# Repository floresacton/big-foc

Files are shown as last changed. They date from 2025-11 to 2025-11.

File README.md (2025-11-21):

# big-foc
Field Oriented Control Inverter

70V 160A 10kW continuous

12kW peak

99% efficiency at 8kW

48$ BOM + PCB Cost

65x75x32mm size

Ignoring the heatsink, that's 64kW/L :)

## Design Strategy

### 1. Power and Voltage Rating
- **Power Rating**: Target continuous and peak power
- **Battery Voltage**: 12S = 50.4V, 16S = 67.2V
- **Component Voltage Rating**: Components must be rated at >1.5x-2x battery voltage
  - Example: 16S battery (67.2V max) → 100V+ rated components minimum
  - Margin for voltage spikes, ringing
- **Thermal Limitation**: Max accepted power dissipation at continuous and peak power, <=100C

### 2. Power Stage Design

#### Switch Selection by Voltage
- **Low Voltage (<300V)**: MOSFETs
  - Aim for lower RDS(on) better conduction losses
  - Aim for lower total gate charge for better switching losses
  - Most cost-effective (100V rated components very common)
- **High Voltage (>300V)**: SiC FETs or IGBTs
  - SiC FETs: Fast switching, lower losses
  - IGBTs: Slower switching, higher switching losses, very high power

#### Gate Driver Selection
- **Bootstrap Drivers**: 
  - Simple, low cost
  - Requires minimum duty cycle for bootstrap to charge
  - Usually fine until back emf approaches battery voltage
  - Pick a fast reverse recovery charge diode
  
- **Isolated Drivers**:
  - Independent high-side supply
  - Usually for high-voltage (>300V)
  - Can handle 100% duty cycle
  - Expensive, more complex

### 3. Power Loss Analysis (very important)

#### Switching Losses
- Target switching frequency from 20-25khz (non audible range & less harmonic distortion)
- Transformers and motors are inductive loads (different switching waveforms than resistive switching loss)
- Switching loss ~= 1/2\*switching frequency\*current*voltage\*(t_on+t_off)
- t_on, t_off ~= Q_gate/I_charge
- I_charge = gate drive current

#### Conduction Losses
- I^2*R × rds_on (for mosfets)
- rds_on increases with temperature so we can use parallel FETs without runaway (thermals matter too)

### 4. Current Sensing

#### Sensing Approach
- **Phase count**:
  - Measure 2 phases calculate third (more noise)
  - Measure 3 phases and average (less noise, better if fits & symmetry)

- **In-Phase**:
  - Able to measures phase currents regardless of switch state
  - Higher cost, a lot of common mode noise
  - Better current measurements if done properly
  
- **Low-Side (1-3 shunts)**:
  - Cheaper
  - Simpler ground referenced amplifier design
  - Can only sample during low side conduction
  - Use stm32 timer ADC synchronization

#### Shunt Resistors
 - Should be around or slightly below rds_on of FETs
 - Good to have about 50-75mV at full current
 - Select for 20V/V amplifier (INA181A1 super common & cheap)
 - <=50ppm for 100C temp rise scenario
 - Need amplifier right next to shunt
 - Need center VREF amp for negative and positive current
 - Need to choose settling time to 1% better than 95% duty cycle (bootstrap is limiting factor)

#### Magnetic Sensing
- Hall-effect sensing built in packages
- Galvanic isolation included
- Higher cost, useful for very high currents
- Minimal power dissipation

### 5. Thermals

#### Power Dissipation Calculation
 - On average 2 half bridges are conducting fully, one is not conducting
- total switching loss ~= 4\*single switch loss
- gate charge loss is usually quite small compared to switching and resistive losses for 25khz
- total conduction loss ~= 2\*single conduction loss

#### FET Cooling Orientation
- **Top-Side Cooling**: FETs mounted with drain pad facing up
  - More expensive
  - Easier to cool and route
  
- **Bottom-Side Cooling**: FETs with dissipation through PCB
  - Cheaper
  - Easier assembly
  - Harder low inductance loop

#### Thermal Design Process
1. Calculate junction-to-case thermal resistance (datasheet)
2. Add PCB thermal resistance
3. Add heatsink thermal resistance
4. Junction temp = Ambient + (Total losses \* Total thermal resistance)
5. Target <100C but <60C is better

### 6. Protection and Sensing

#### Temperature Monitoring
- NTC thermistor (cheaper than PTC) on heatsink or FETs
- Lower B kind of better like 3400 because more linear over big range
- 10k 3400B ~= 1k at 100C, 30k at 0C

#### Fast Overvoltage Protection
- Hardware comparator for <1µs response time
- Trigger emergency PWM shutdown (stm32 timer break input)
- Threshold = 0.9% or something of voltage rating
- Directly disables gate drivers
- Optional avalanche diode for last resort protection

#### Voltage Measurement
- Resistor divider to ADC with a little bit of filtering
- Per-phase voltage for locking onto back emf for high speed

### 7. Microcontroller Selection

#### STM32G4 Series
**Key Features for FOC:**
- High-resolution timers with dead-time insertion and center aligned PWM
- Fast 12-bit ADCs
- ADC triggering synchronized to PWM for current sampling
- Multiple ADCs for simultaneous phase current sampling
- Math acceleration (FPU, CORDIC) for FOC
- Sufficient for >20kHz control loop

**Typical MCU Choices:**
- STM32G431: Small packages, cost-optimized
- STM32G474: More peripherals, flash, and RAM for complex algorithms

### 8. FOC Control Implementation

#### Control Loop Structure
- Current loop: 10-50kHz (1/10 of switching frequency typical)
- Velocity loop: 1-5kHz
- Position loop: 100-1000Hz

#### Key Considerations
- ADC sampling synchronized to PWM valley/center
- Current reconstruction for low-side shunts
- PI controller tuning based on motor parameters
- Clarke/Park transforms for coordinate conversion
- Space Vector Modulation (SVM) for efficient bus utilization
- Add third harmonic for higher effective bus voltage

### 9. PCB Layout (Very very important)
 - Low inductance switching loop
 - di/dt \* L = voltage induced over drain source
 - Low esr (usually MLCC) caps in low inductance switching loop
 - very rough calc Q_sustain = t_deadtime*I_peak
 - Q_sustain / V_spike = C_switch loop
 - Goal to hit V_spike <1% of V_bus
 - Keep loops as small as possible
 - Shunt amplifier right next to shunt resistor

### 10. Connectors
 - Waterproof, either SD13 series or DT Duetch (orange ones) are common
 - Phase and power wires just shrouded, bolt internally

### 11. Example Calculations (for my inverter)
- **Motor Characteristics**
	- 40uH phase to phase inductance
	- AMKs have 2.5nF inter winding capacitance
	- Couldn't find inter-winding capacitance of mine, but I think its relatively small losses compared to conduction
- [MOSFET loss equations](https://www.ti.com/lit/an/slyt664/slyt664.pdf?ts=1762657470589)
- [Layout and more equations](https://www.infineon.com/assets/row/public/documents/24/42/infineon-designing-an-optimized-half-bridge-dc-dc-converter-with-medium-voltage-coolgan-transistors-applic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)
 - **Losses**
	 - Power 8.4kW at 120A rms current or two phases at 170A
	 - 2 phases on at a time on average (same thing as 3 RMS currents)
	 - parallel rds @ 15V: 0.55mohm at 25C, 0.85mohm at 100C
	 - P_cond_tot = 2\*170\*170\*0.00055 = 32W
	 - P_shunt = 2\*170\*170\*0.00033 = 19W
	 - Q_gs2 = 20nC, Q_gd = 50nC, Q_eff = 70nC
	 - Q_actual = 140nC cause parallel FETs
	 - P_sw = 2\*70V\*170A\*25khz\*140nC/4A = 20.8W
	 - P_sw_total = 8.925W\*2 half bridge = 41.6W
     - P_recovery = 25khz\*200nC\*70V*8FETs = 2.8W
	 - P_coss = 12FETs \* 25khz \* 70V^2 \* 2.3nF = 3.4W
	 - P_winding_cap = 3 phase \* 25khz \* 70V^2 \* 2.5nF = 0.9W
	 - P_gate_total = 12 FETs\*250nC\*15V\*25khz = 1.1W
	 - P_gate_drive = <1W
	 - Deadtime 150ns
	 - P_diode = ~1.5\*1.2V\*170A\*25khz\*150ns = 1.2W (a bit sus math but reasonable)
	 - 4% dissipation factor for 1206 2.2uF ~ 10mohm I think for equivalent 10 (randomish number)
	 - Sw_energy = 70V\*170A\*140nC/4A = 0.4mJ per phase
	 - C_droop ~= 0.4mJ/(20uF \* 70V) = 0.3V
	 - The Vrms of the droop is prob below ~50mV
	 - P_cap_sw = 50mV^2/10mohm = 0.25W*3phases comes to <1W
	 - I_ripple ~= 110A
	 - Assuming 70A into ceramics and 40A into electrolytic
	 - 80 ceramics / 70A = 0.87A per ceramic
	 - P_ripple_cer = 0.875^2 \* 100mohm = 80mW
	 - P_cer_tot = 0.08*80 = 6.4W
	 - Electrolytic 3mohm at 25khz (susish think ok)
	 - I_elec ~= 40A/10 = 4A
	 - P_elec = 4A^2 \* 3mohm = 48mW
	 - P_elec_tot = 48mW \* 10 = 0.5W
	 - Total at 8.4kW = 32+41.6+1.1+1.2+1+1+6.4+0.5+3.4+19+2.8= 109.9W
	 - About 98.6% efficiency
- **Control**
	- Max phase current 220A, 210A max (170rms) is 12kW
	- SVPWM
	- Optional 3rd harmonic overmodulation
	- I_phase_rms = I_phase_pk / sqrt(12)
	- I_pk_pk_ripple = 70V / (2 \* 40uH \* 25khz) \* D \* (1-D) = 8.75A ; D=0.5
	- I_pk = 4.4A
	- I_rms = I_pk_pk_ripple / sqrt(12) = 2.5A

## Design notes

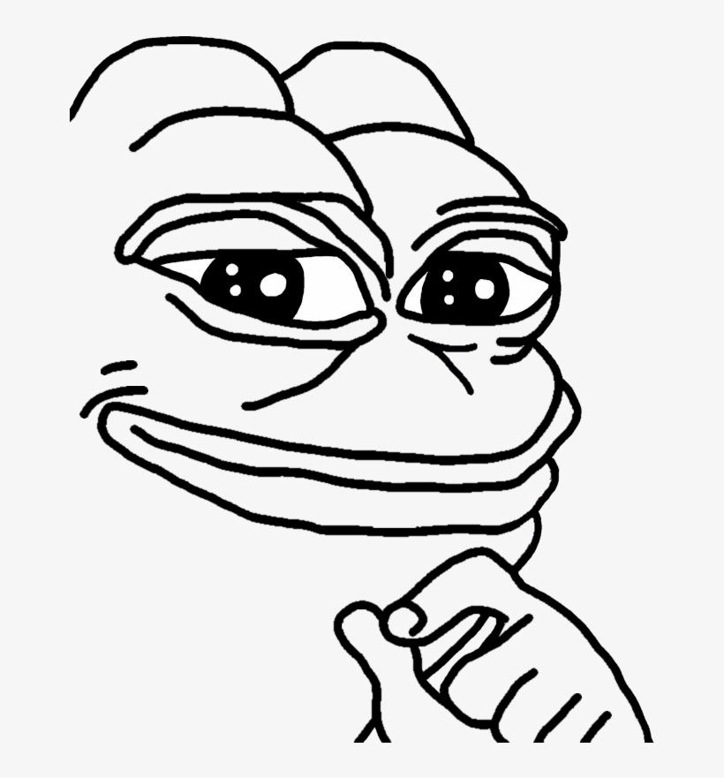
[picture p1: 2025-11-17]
pcb/logic/smart-pepe.jpg

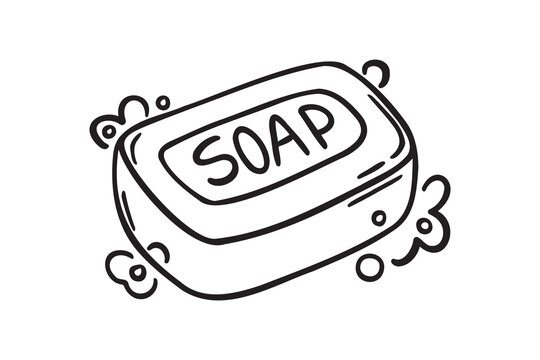
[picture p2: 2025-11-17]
pcb/logic/soap.jpg

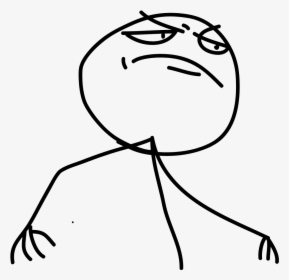
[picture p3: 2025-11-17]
pcb/logic/stickman-showoff.jpg

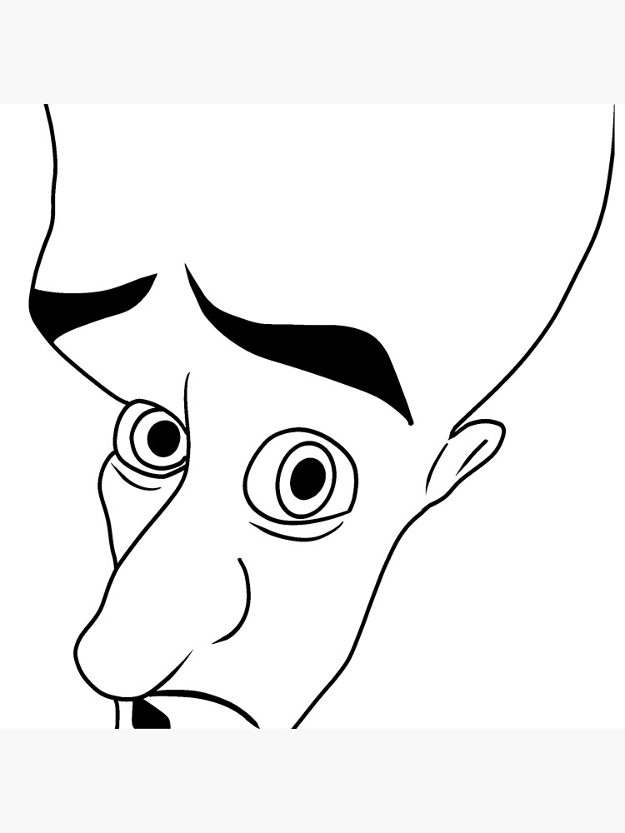
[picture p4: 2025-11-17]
pcb/logic/megamind.jpg

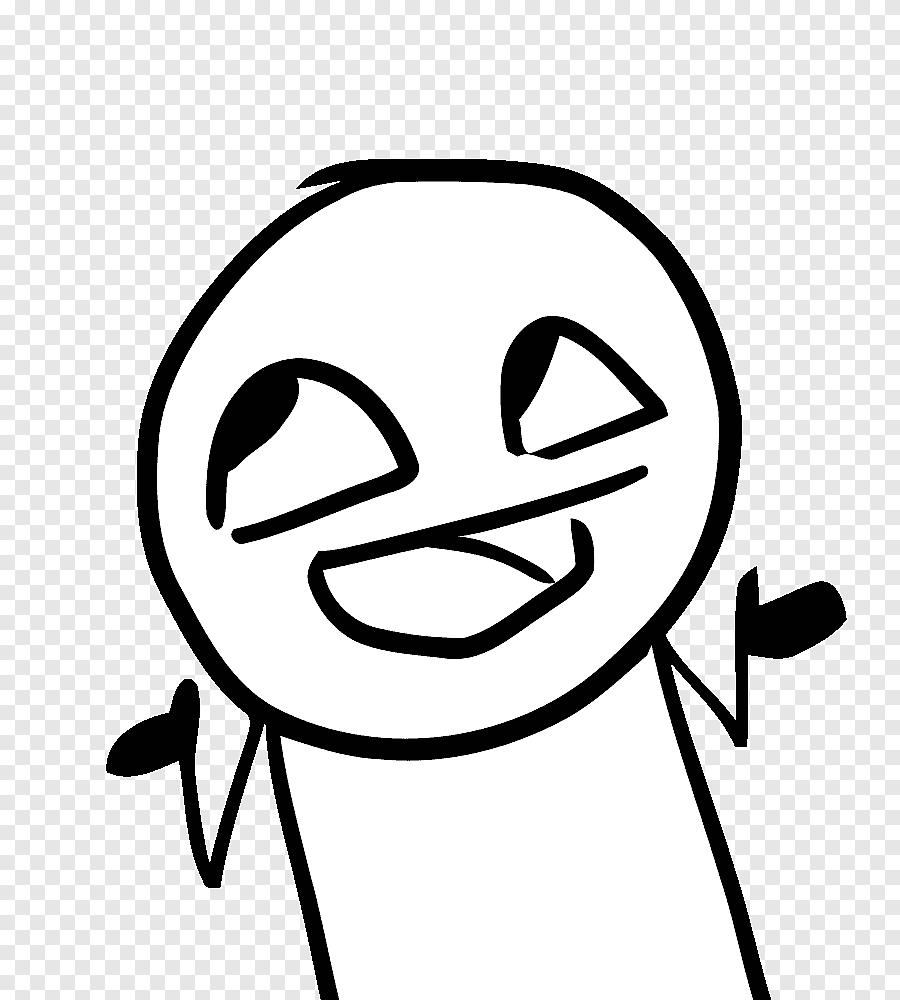
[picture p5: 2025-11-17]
pcb/logic/iguess.png

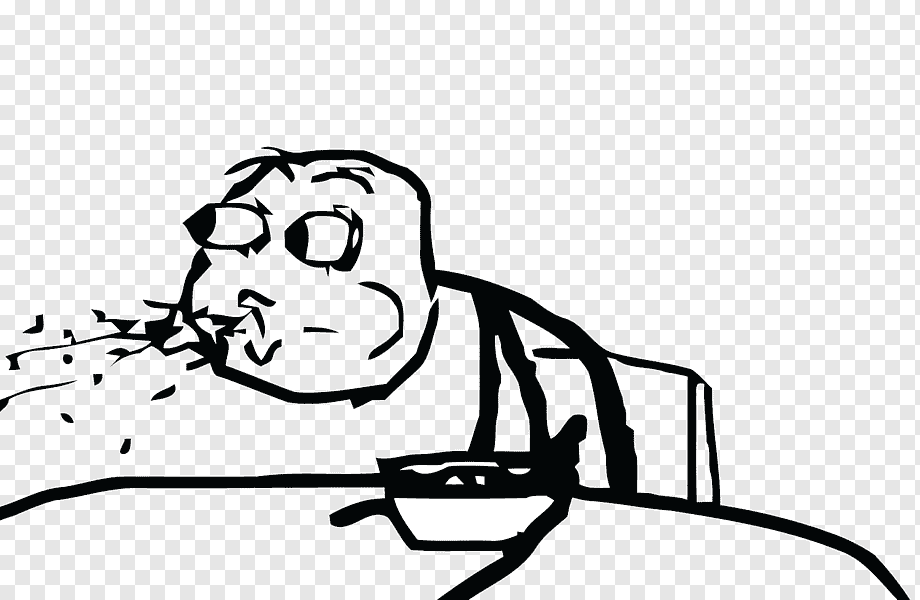
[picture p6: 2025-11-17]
pcb/logic/surprised.png

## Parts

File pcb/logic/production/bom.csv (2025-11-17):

Designator | Footprint | Quantity | Value | LCSC Part #
C1, C2, C3 | 1206 | 3 | 4u7 | C29823
C10, C11, C12, C13, C14, C15, C16, C19, C34, C35, C36, C37, C38, C39, C41, C42, C43, C44, C46, C47, C48, C49, C50, C52, C54, C55, C7, C8, C9 | 0402 | 29 | 100n | C307331
C17, C4, C5, C6 | 0402 | 4 | 220p | C1530
C18, C25, C26, C27, C28, C29, C30 | 0402 | 7 | 10n | C15195
C20, C40, C57 | 1206 | 3 | 22u | C20416445
C21, C22, C23, C24, C45, C56, C59 | 0805 | 7 | 4u7 | C33546011
C31, C32, C33, C58 | 0402 | 4 | 1n | C1523
C51, C53 | 0402 | 2 | 10p | C32949
D1 | 0603 | 1 | LED | C2290
D4, D5, D6 | D_SOD-323 | 3 | 1N4148WS | C2128
FB1 | 0603 | 1 | 120 | C14709
J1, J3, J5 | PinSocket_2x02_P1.27mm_Vertical_SMD | 3 | Conn_02x02_Odd_Even | C30607465
J2, J4, J6 | PinSocket_2x03_P1.27mm_Vertical_SMD | 3 | Conn_02x03_Odd_Even | C32713074
L2 | L_TechFuse_SL0420 | 1 | 4u7 | C22463808
R1, R11, R13, R2, R26, R27, R28, R3, R30, R33, R34 | 0402 | 11 | 33k | C25779
R10, R12, R14, R15, R16, R17, R29, R31, R35, R36, R37, R38, R4, R40, R41, R42, R43, R5, R6, R7, R8, R9 | 0402 | 22 | 2k2 | C25879
R18, R19, R20, R21, R22, R23 | 0603 | 6 | 1 | C22936
R24, R25 | 0805 | 2 | 51 | C17738
R32 | 0402 | 1 | 330 | C25104
R39 | 0402 | 1 | 12k | C25752
TH1, TH2, TH3, TH4 | 0402 | 4 | 10k | C41417281
U1, U2, U3 | JEITA_SOIC-8_3.9x4.9mm_P1.27mm | 3 | IRS2181STR | C20623180
U10, U11, U12, U13, U8, U9 | SOT-23-5 | 6 | 74LVC1G66 | C46553572
U14 | SOT-23-6 | 1 | JW5017S | C371172
U4 | SOT-223-3_TabPin2 | 1 | AMS1117-3.3 | C6186
U5 | LQFP-48_7x7mm_P0.5mm | 1 | STM32G473CBTx | C730111
U6 | JEITA_SOIC-8_3.9x4.9mm_P1.27mm | 1 | SP485E | C6855
Y1 | Crystal_SMD_3225-4Pin_3.2x2.5mm | 1 | 16MHz | C13738

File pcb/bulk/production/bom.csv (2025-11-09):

Designator | Footprint | Quantity | Value | LCSC Part #
C1, C10, C11, C12, C13, C14, C15, C16, C17, C18, C19, C2, C20, C21, C22, C23, C24, C25, C26, C27, C28, C29, C3, C30, C31, C32, C33, C34, C35, C36, C37, C38, C39, C4, C40, C41, C42, C43, C44, C45, C46, C47, C48, C49, C5, C50, C51, C52, C53, C54, C55, C56, C57, C58, C59, C6, C60, C61, C62, C63, C64, C65, C66, C67, C68, C69, C7, C70, C71, C72, C73, C74, C75, C76, C77, C78, C79, C8, C80, C81, C9 | 1206 | 81 | 2u2 | C920964
C82, C83, C84, C85, C86 | C_Radial_D10.0mm_H20.0mm_P5.00mm | 5 | 100u | C106541
C87, C88, C89, C90, C91, C92, C93, C94 | C_Radial_D12.5mm_H20.0mm_P5.00mm | 8 | 220u | C5213780

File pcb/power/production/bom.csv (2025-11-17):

Designator | Footprint | Quantity | Value | LCSC Part #
C1, C11, C21 | 0402 | 3 | 100n | C1525
C10, C12, C13, C14, C15, C16, C17, C18, C19, C2, C20, C22, C23, C24, C25, C26, C27, C28, C29, C3, C30, C4, C5, C6, C7, C8, C9 | 1206 | 27 | 2u2 | C920964
J1, J3, J5 | PinHeader_2x02_P1.27mm_Vertical_SMD | 3 | Conn_02x02_Odd_Even | C27985143
J2, J4, J6 | PinHeader_2x03_P1.27mm_Vertical_SMD | 3 | Conn_02x03_Odd_Even | C27985144
Q1, Q10, Q11, Q12, Q2, Q3, Q4, Q5, Q6, Q7, Q8, Q9 | Infineon_PG-HSOF-8-1 | 12 | SP010N01BGHTO | C22385350
R1, R2, R3, R4, R5, R6, R7, R8, R9 | R_Shunt_3921 | 9 | 1m | C2927603
U1, U2, U3 | SOT-23-6 | 3 | INA181 | C52097916

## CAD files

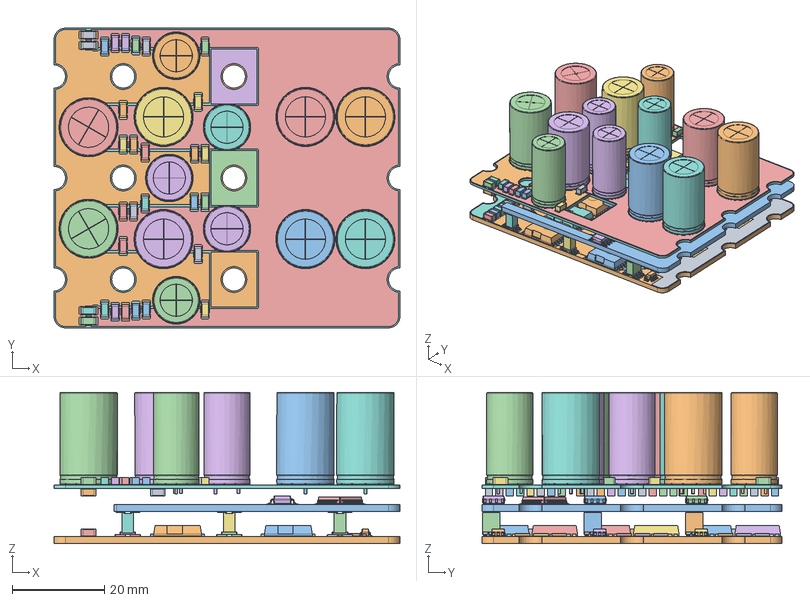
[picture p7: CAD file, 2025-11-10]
pcb/assembly.fcstd
75.0 x 65.0 x 32.8 mm
PinHeader_2x03_P1.27mm_Vertical_SMD
C_1206_3216Metric081
C_1206_3216Metric082
C_1206_3216Metric083
power 1.5.1
power 1.5.002
power 1.5.003
power 1.5.004
power 1.5.005
power 1.5.006
power 1.5.007
power 1.5.008
power 1.5.009
power 1.5.010
R_2512_6332Metric
power 1.5.012
power 1.5.013
power 1.5.014
power 1.5.015
power 1.5.016
power 1.5.017
power 1.5.018
power 1.5.019
power 1.5.020
power 1.5.021
R_2512_6332Metric001
power 1.5.023
power 1.5.024
power 1.5.025
power 1.5.026
power 1.5.027
power 1.5.028
power 1.5.029
power 1.5.030
power 1.5.031
power 1.5.032
C_1206_3216Metric084
C_1206_3216Metric085
power 1.5.034
power 1.5.035
power 1.5.036
power 1.5.037
power 1.5.038
power 1.5.039
power 1.5.040
power 1.5.041
power 1.5.042
power 1.5.043
C_1206_3216Metric086
power 1.5.045
power 1.5.046
power 1.5.047
power 1.5.048
power 1.5.049
power 1.5.050
power 1.5.051
power 1.5.052
power 1.5.053
power 1.5.054
C_1206_3216Metric087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

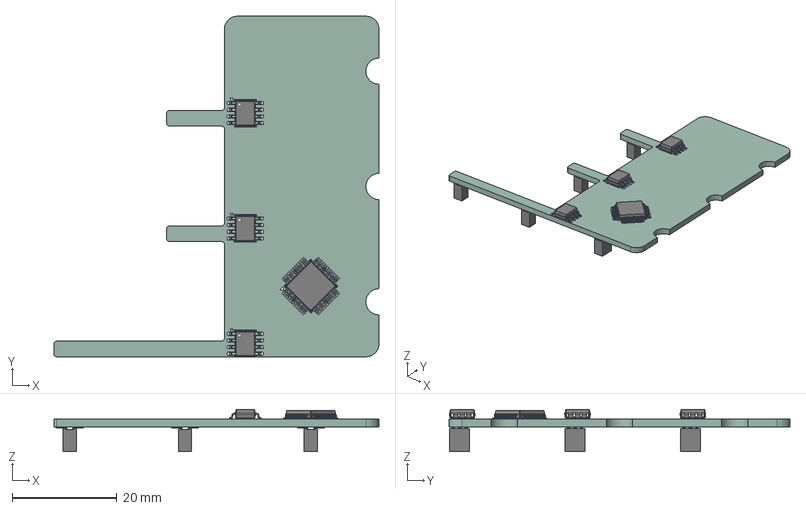
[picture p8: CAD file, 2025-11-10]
pcb/logic/logic.step
62.0 x 65.0 x 8.04 mm
SOIC-8_3.9x4.9mm_P1.27mm x 3
LQFP-48_7x7mm_P0.5mm
PinSocket_2x02_P1.27mm_Vertical_SMD x 4
PinSocket_2x03_P1.27mm_Vertical_SMD x 3
logic_pad
logic_silkscreen x 2
logic_PCB

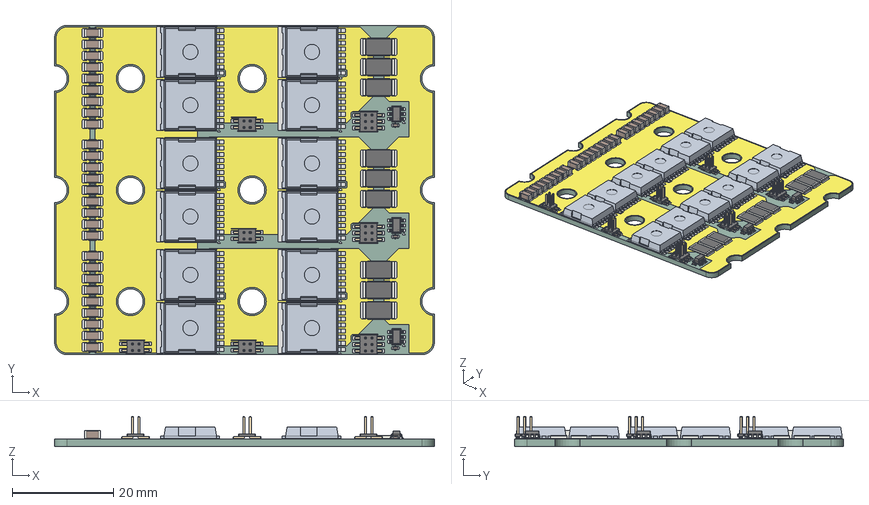
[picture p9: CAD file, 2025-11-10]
pcb/power/power.step
75.0 x 65.0 x 5.99 mm
PinHeader_2x03_P1.27mm_Vertical_SMD x 3
C_1206_3216Metric x 27
power 1.5.1 x 12
R_2512_6332Metric x 9
C_0402_1005Metric x 3
PinHeader_2x02_P1.27mm_Vertical_SMD x 4
SOT-23-6 x 3
power_copper
power_pad
power_silkscreen
power_PCB

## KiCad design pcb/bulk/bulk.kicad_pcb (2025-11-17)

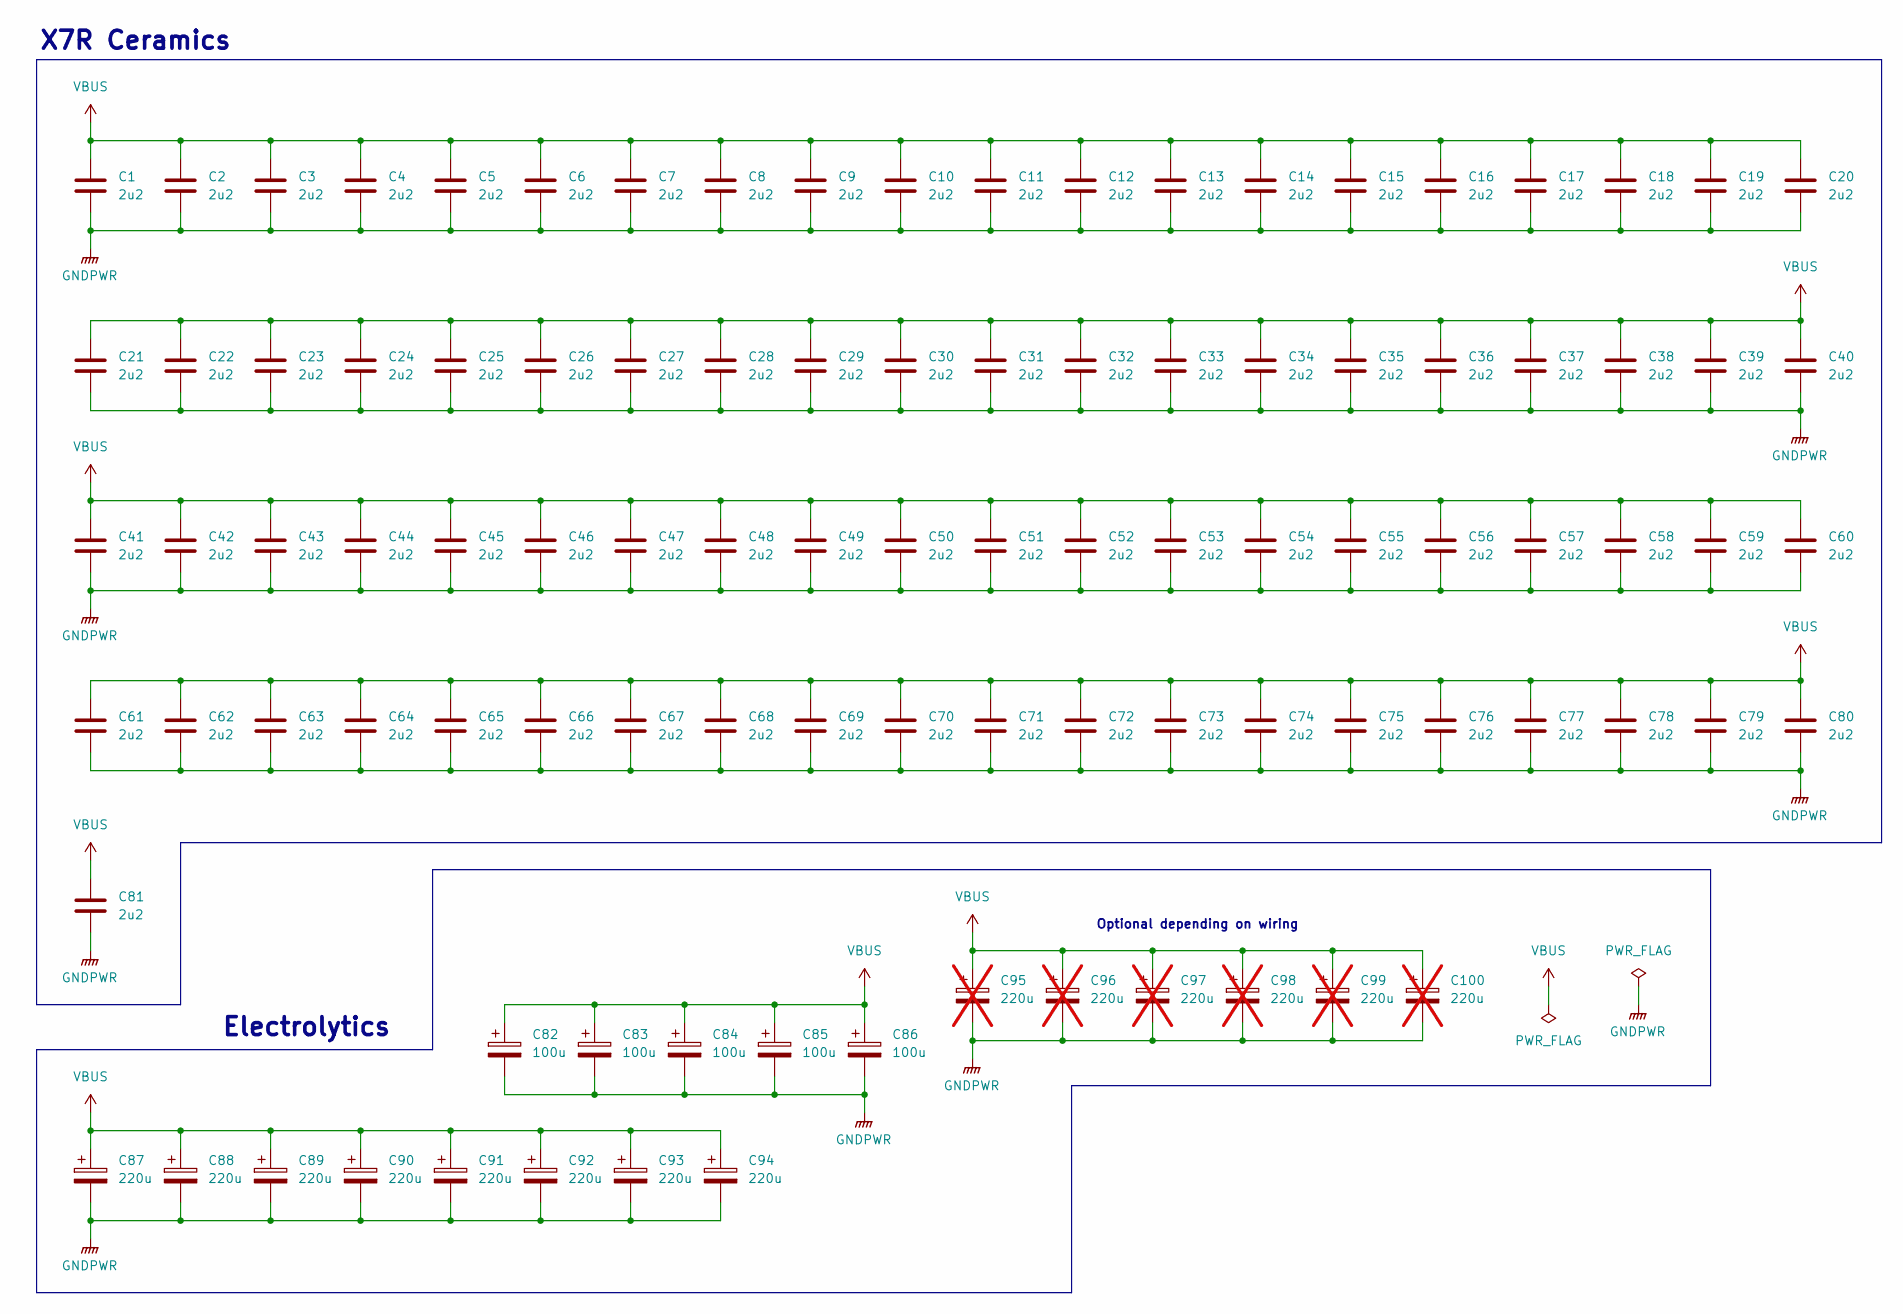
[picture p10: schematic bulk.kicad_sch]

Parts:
C1, C2, C3, C4, C5, C6, C7, C8, C9, C10, C11, C12, C13, C14, C15, C16, C17, C18, C19, C20, C21, C22, C23, C24, C25, C26, C27, C28, C29, C30, C31, C32, C33, C34, C35, C36, C37, C38, C39, C40, C41, C42, C43, C44, C45, C46, C47, C48, C49, C50, C51, C52, C53, C54, C55, C56, C57, C58, C59, C60, C61, C62, C63, C64, C65, C66, C67, C68, C69, C70, C71, C72, C73, C74, C75, C76, C77, C78, C79, C80, C81: 2u2; C_1206_3216Metric; LCSC C920964
C82, C83, C84, C85, C86: 100u; C_Radial_D10.0mm_H20.0mm_P5.00mm; LCSC C106541
C87, C88, C89, C90, C91, C92, C93, C94: 220u; C_Radial_D12.5mm_H20.0mm_P5.00mm; LCSC C5213780
C95, C96, C97, C98, C99, C100: 220u; C_Radial_D12.5mm_H20.0mm_P5.00mm; LCSC C5213780; not fitted

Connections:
GNDPWR: C1.2, C2.2, C3.2, C4.2, C5.2, C6.2, C7.2, C8.2, C9.2, C10.2, C11.2, C12.2, C13.2, C14.2, C15.2, C16.2, C17.2, C18.2, C19.2, C20.2, C21.2, C22.2, C23.2, C24.2, C25.2, C26.2, C27.2, C28.2, C29.2, C30.2, C31.2, C32.2, C33.2, C34.2, C35.2, C36.2, C37.2, C38.2, C39.2, C40.2, C41.2, C42.2, C43.2, C44.2, C45.2, C46.2, C47.2, C48.2, C49.2, C50.2, C51.2, C52.2, C53.2, C54.2, C55.2, C56.2, C57.2, C58.2, C59.2, C60.2, C61.2, C62.2, C63.2, C64.2, C65.2, C66.2, C67.2, C68.2, C69.2, C70.2, C71.2, C72.2, C73.2, C74.2, C75.2, C76.2, C77.2, C78.2, C79.2, C80.2, C81.2, C82.2, C83.2, C84.2, C85.2, C86.2, C87.2, C88.2, C89.2, C90.2, C91.2, C92.2, C93.2, C94.2, C95.2, C96.2, C97.2, C98.2, C99.2, C100.2
VBUS: C1.1, C2.1, C3.1, C4.1, C5.1, C6.1, C7.1, C8.1, C9.1, C10.1, C11.1, C12.1, C13.1, C14.1, C15.1, C16.1, C17.1, C18.1, C19.1, C20.1, C21.1, C22.1, C23.1, C24.1, C25.1, C26.1, C27.1, C28.1, C29.1, C30.1, C31.1, C32.1, C33.1, C34.1, C35.1, C36.1, C37.1, C38.1, C39.1, C40.1, C41.1, C42.1, C43.1, C44.1, C45.1, C46.1, C47.1, C48.1, C49.1, C50.1, C51.1, C52.1, C53.1, C54.1, C55.1, C56.1, C57.1, C58.1, C59.1, C60.1, C61.1, C62.1, C63.1, C64.1, C65.1, C66.1, C67.1, C68.1, C69.1, C70.1, C71.1, C72.1, C73.1, C74.1, C75.1, C76.1, C77.1, C78.1, C79.1, C80.1, C81.1, C82.1, C83.1, C84.1, C85.1, C86.1, C87.1, C88.1, C89.1, C90.1, C91.1, C92.1, C93.1, C94.1, C95.1, C96.1, C97.1, C98.1, C99.1, C100.1

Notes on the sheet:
X7R Ceramics
Optional depending on wiring
Electrolytics

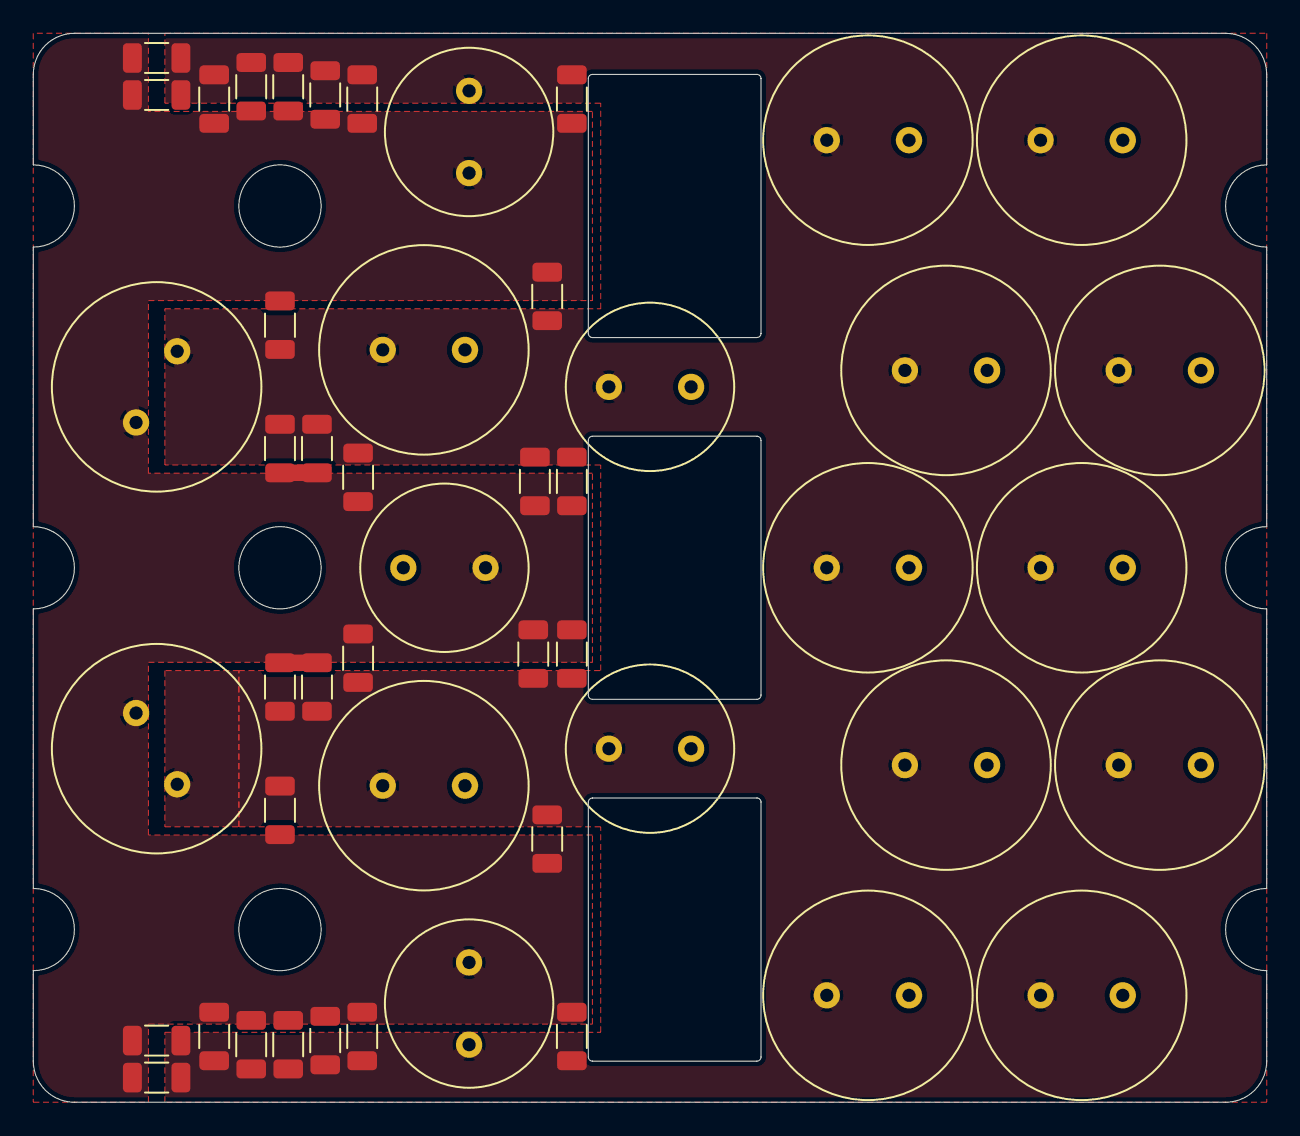
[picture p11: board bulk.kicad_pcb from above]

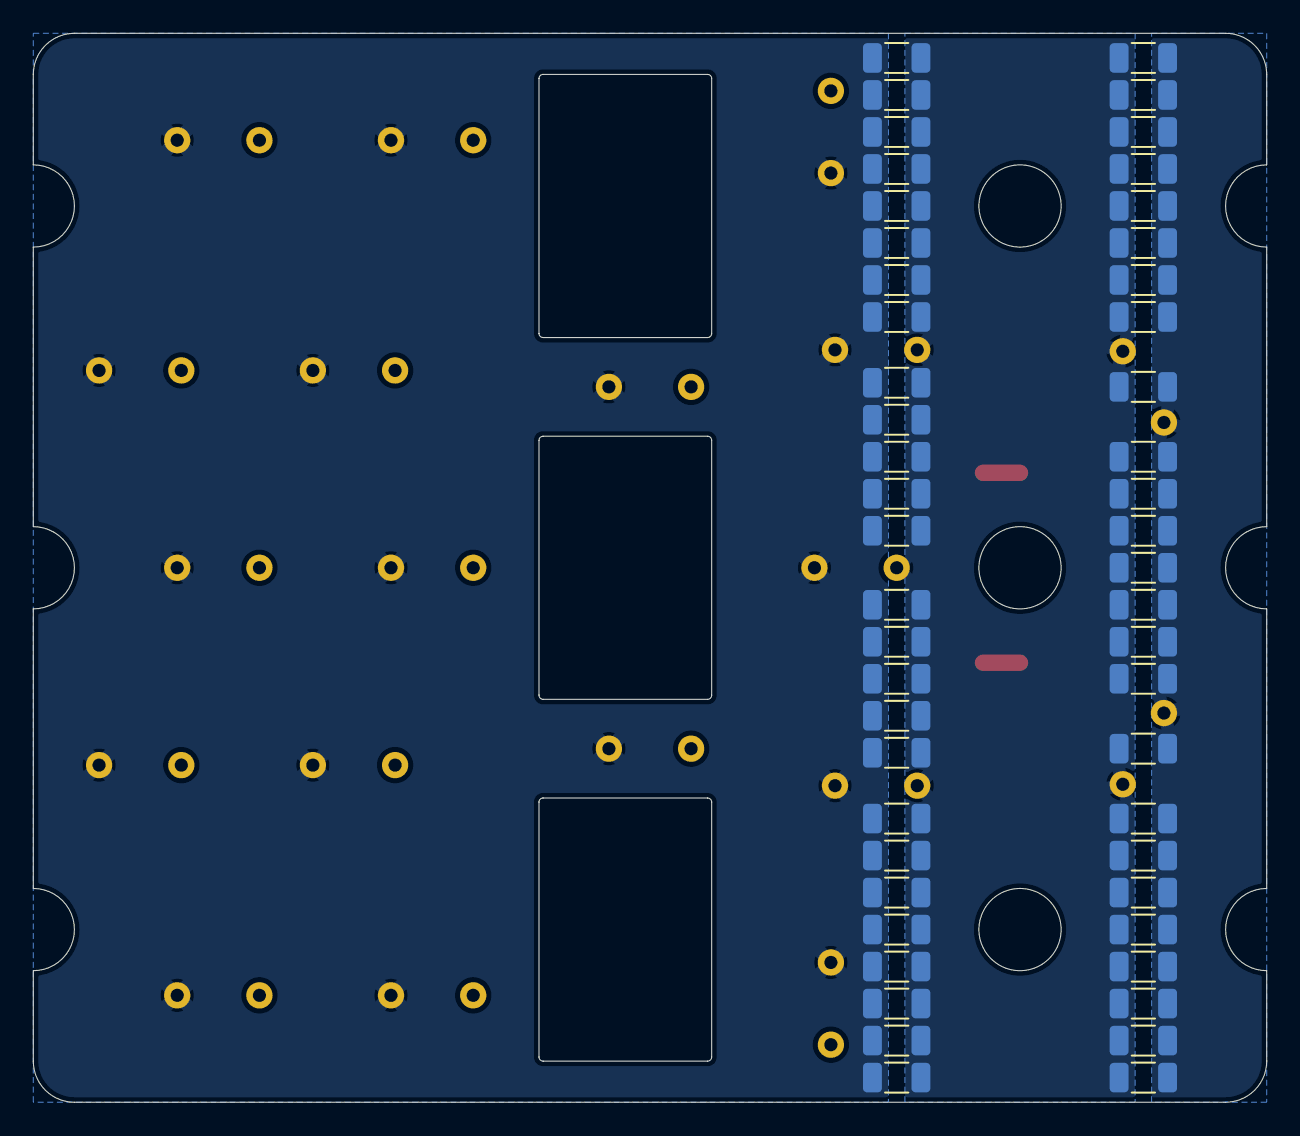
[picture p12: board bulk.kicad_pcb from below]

Board: 2 copper layers, 75.0 x 65.0 mm, 100 parts (51 on the bottom side), 2 nets.

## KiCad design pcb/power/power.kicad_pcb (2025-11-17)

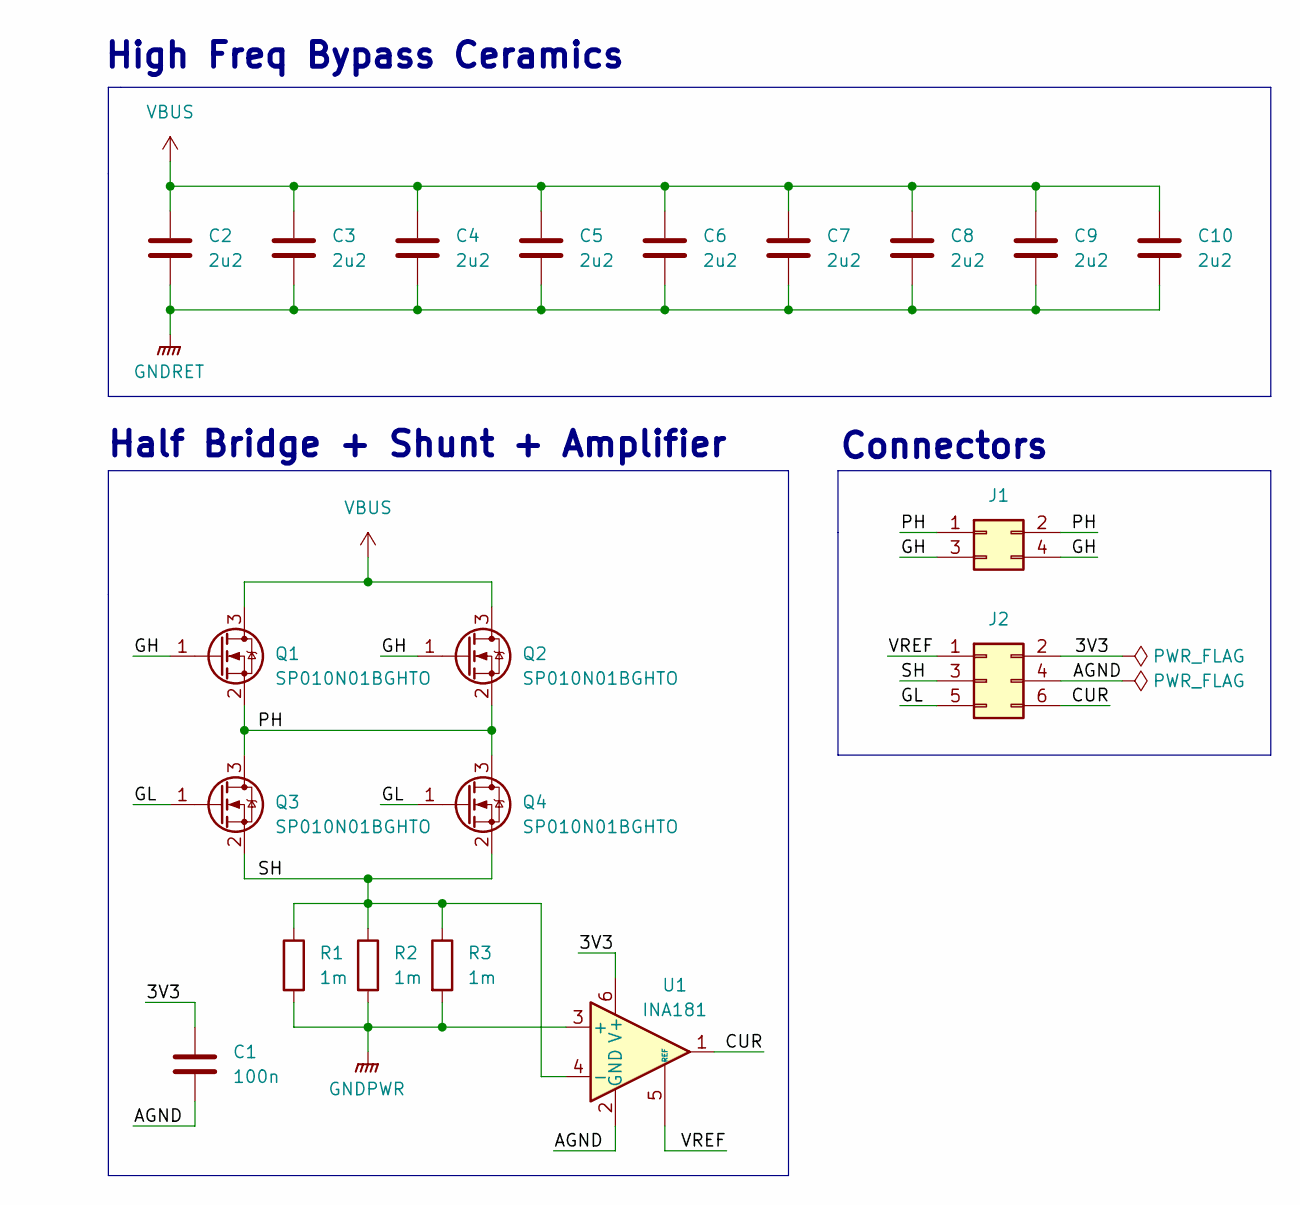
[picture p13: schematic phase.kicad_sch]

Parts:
C1: 100n; C_0402_1005Metric; LCSC C307331
C2, C3, C4, C5, C6, C7, C8, C9, C10: 2u2; C_1206_3216Metric; LCSC C920964
J1: Conn_02x02_Odd_Even; PinHeader_2x02_P1.27mm_Vertical_SMD; LCSC C27985143
J2: Conn_02x03_Odd_Even; PinHeader_2x03_P1.27mm_Vertical_SMD; LCSC C27985144
Q1, Q2, Q3, Q4: SP010N01BGHTO; Infineon_PG-HSOF-8-1; LCSC C22385350
R1, R2, R3: 1m; R_Shunt_3921; LCSC C2927603
U1: INA181; SOT-23-6; LCSC C52097916

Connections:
/Phase1/3V3: C1.1, J2.2, U1.6 (V+)
/Phase1/AGND: C1.2, J2.4, U1.2 (GND)
/Phase1/CUR: J2.6, U1.1
/Phase1/GH: J1.3, J1.4, Q1.1 (G), Q2.1 (G)
/Phase1/GL: J2.5, Q3.1 (G), Q4.1 (G)
/Phase1/PH: J1.1, J1.2, Q1.2 (S), Q2.2 (S), Q3.3 (D), Q4.3 (D)
/Phase1/SH: J2.3, Q3.2 (S), Q4.2 (S), R1.1, R2.1, R3.1, U1.4 (-)
/Phase1/VREF: J2.1, U1.5 (REF)
GNDPWR: R1.2, R2.2, R3.2, U1.3 (+); also elsewhere on the board
GNDRET: C2.2, C3.2, C4.2, C5.2, C6.2, C7.2, C8.2, C9.2, C10.2; also elsewhere on the board
VBUS: C2.1, C3.1, C4.1, C5.1, C6.1, C7.1, C8.1, C9.1, C10.1, Q1.3 (D), Q2.3 (D); also elsewhere on the board

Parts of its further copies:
C11, C21: 100n; C_0402_1005Metric; LCSC C307331
C12, C13, C14, C15, C16, C17, C18, C19, C20, C22, C23, C24, C25, C26, C27, C28, C29, C30: 2u2; C_1206_3216Metric; LCSC C920964
J3, J5: Conn_02x02_Odd_Even; PinHeader_2x02_P1.27mm_Vertical_SMD; LCSC C27985143
J4, J6: Conn_02x03_Odd_Even; PinHeader_2x03_P1.27mm_Vertical_SMD; LCSC C27985144
Q5, Q6, Q7, Q8, Q9, Q10, Q11, Q12: SP010N01BGHTO; Infineon_PG-HSOF-8-1; LCSC C22385350
R4, R5, R6, R7, R8, R9: 1m; R_Shunt_3921; LCSC C2927603
U2, U3: INA181; SOT-23-6; LCSC C52097916

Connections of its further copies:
/Phase2/3V3: C11.1, J4.2, U2.6 (V+)
/Phase2/AGND: C11.2, J4.4, U2.2 (GND)
/Phase2/CUR: J4.6, U2.1
/Phase2/GH: J3.3, J3.4, Q5.1 (G), Q6.1 (G)
/Phase2/GL: J4.5, Q7.1 (G), Q8.1 (G)
/Phase2/PH: J3.1, J3.2, Q5.2 (S), Q6.2 (S), Q7.3 (D), Q8.3 (D)
/Phase2/SH: J4.3, Q7.2 (S), Q8.2 (S), R4.1, R5.1, R6.1, U2.4 (-)
/Phase2/VREF: J4.1, U2.5 (REF)
/Phase3/3V3: C21.1, J6.2, U3.6 (V+)
/Phase3/AGND: C21.2, J6.4, U3.2 (GND)
/Phase3/CUR: J6.6, U3.1
/Phase3/GH: J5.3, J5.4, Q9.1 (G), Q10.1 (G)
/Phase3/GL: J6.5, Q11.1 (G), Q12.1 (G)
/Phase3/PH: J5.1, J5.2, Q9.2 (S), Q10.2 (S), Q11.3 (D), Q12.3 (D)
/Phase3/SH: J6.3, Q11.2 (S), Q12.2 (S), R7.1, R8.1, R9.1, U3.4 (-)
/Phase3/VREF: J6.1, U3.5 (REF)
GNDPWR: R4.2, R5.2, R6.2, R7.2, R8.2, R9.2, U2.3 (+), U3.3 (+); also elsewhere on the board
GNDRET: C12.2, C13.2, C14.2, C15.2, C16.2, C17.2, C18.2, C19.2, C20.2, C22.2, C23.2, C24.2, C25.2, C26.2, C27.2, C28.2, C29.2, C30.2; also elsewhere on the board
VBUS: C12.1, C13.1, C14.1, C15.1, C16.1, C17.1, C18.1, C19.1, C20.1, C22.1, C23.1, C24.1, C25.1, C26.1, C27.1, C28.1, C29.1, C30.1, Q5.3 (D), Q6.3 (D), Q9.3 (D), Q10.3 (D); also elsewhere on the board

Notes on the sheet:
High Freq Bypass Ceramics
Connectors
Half Bridge + Shunt + Amplifier

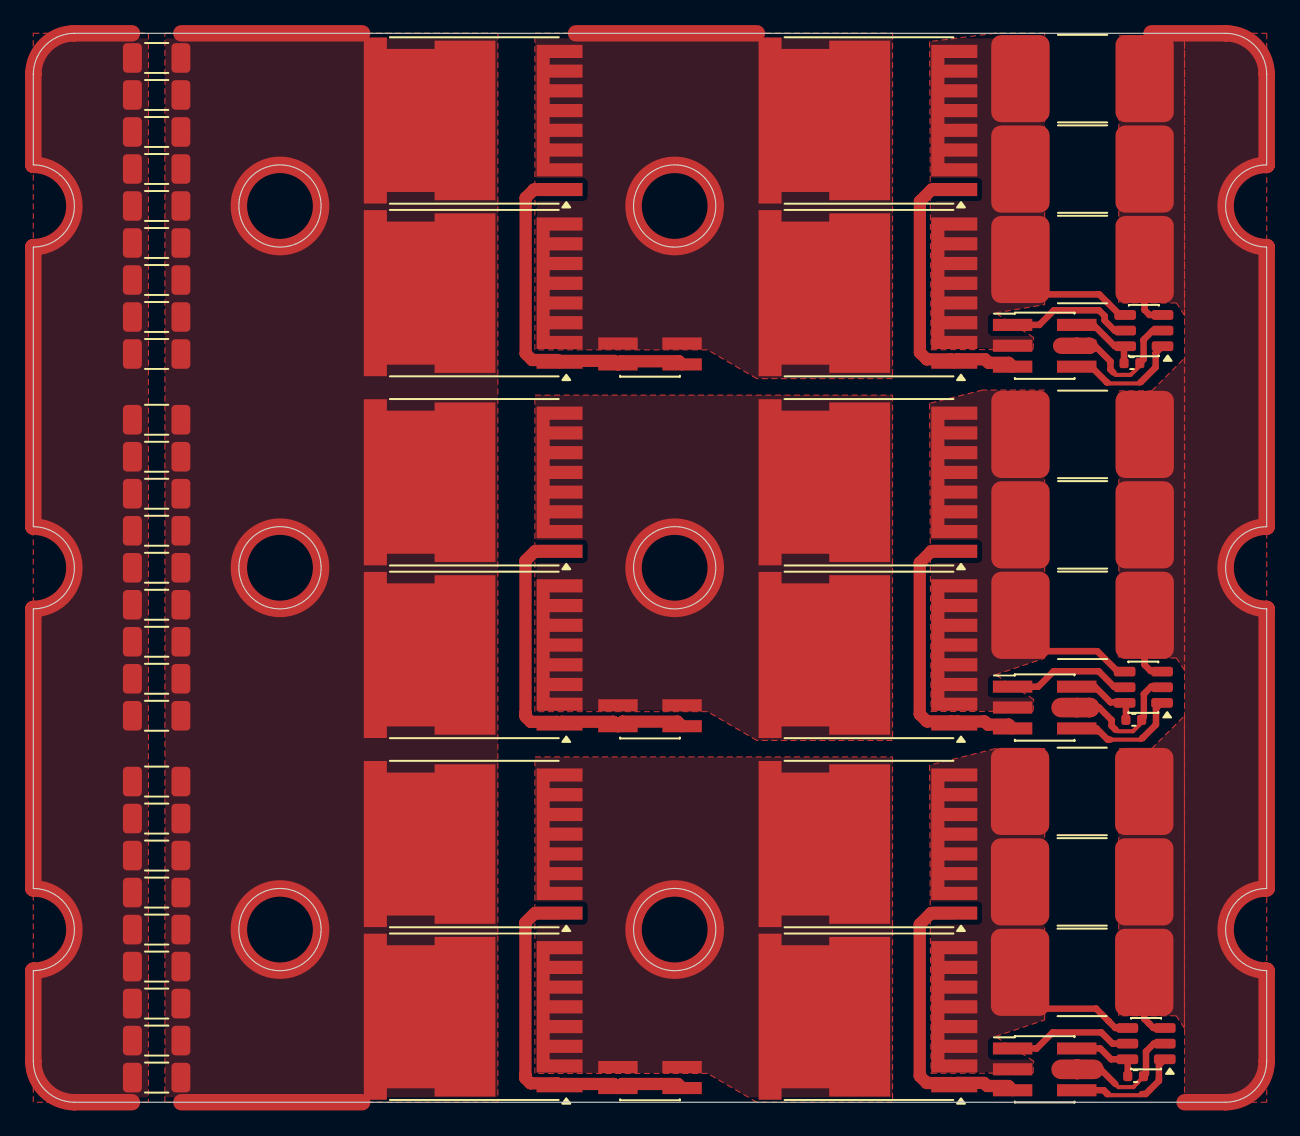
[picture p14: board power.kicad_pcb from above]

Board: 2 copper layers, 75.0 x 65.0 mm, 60 parts (0 on the bottom side), 27 nets.

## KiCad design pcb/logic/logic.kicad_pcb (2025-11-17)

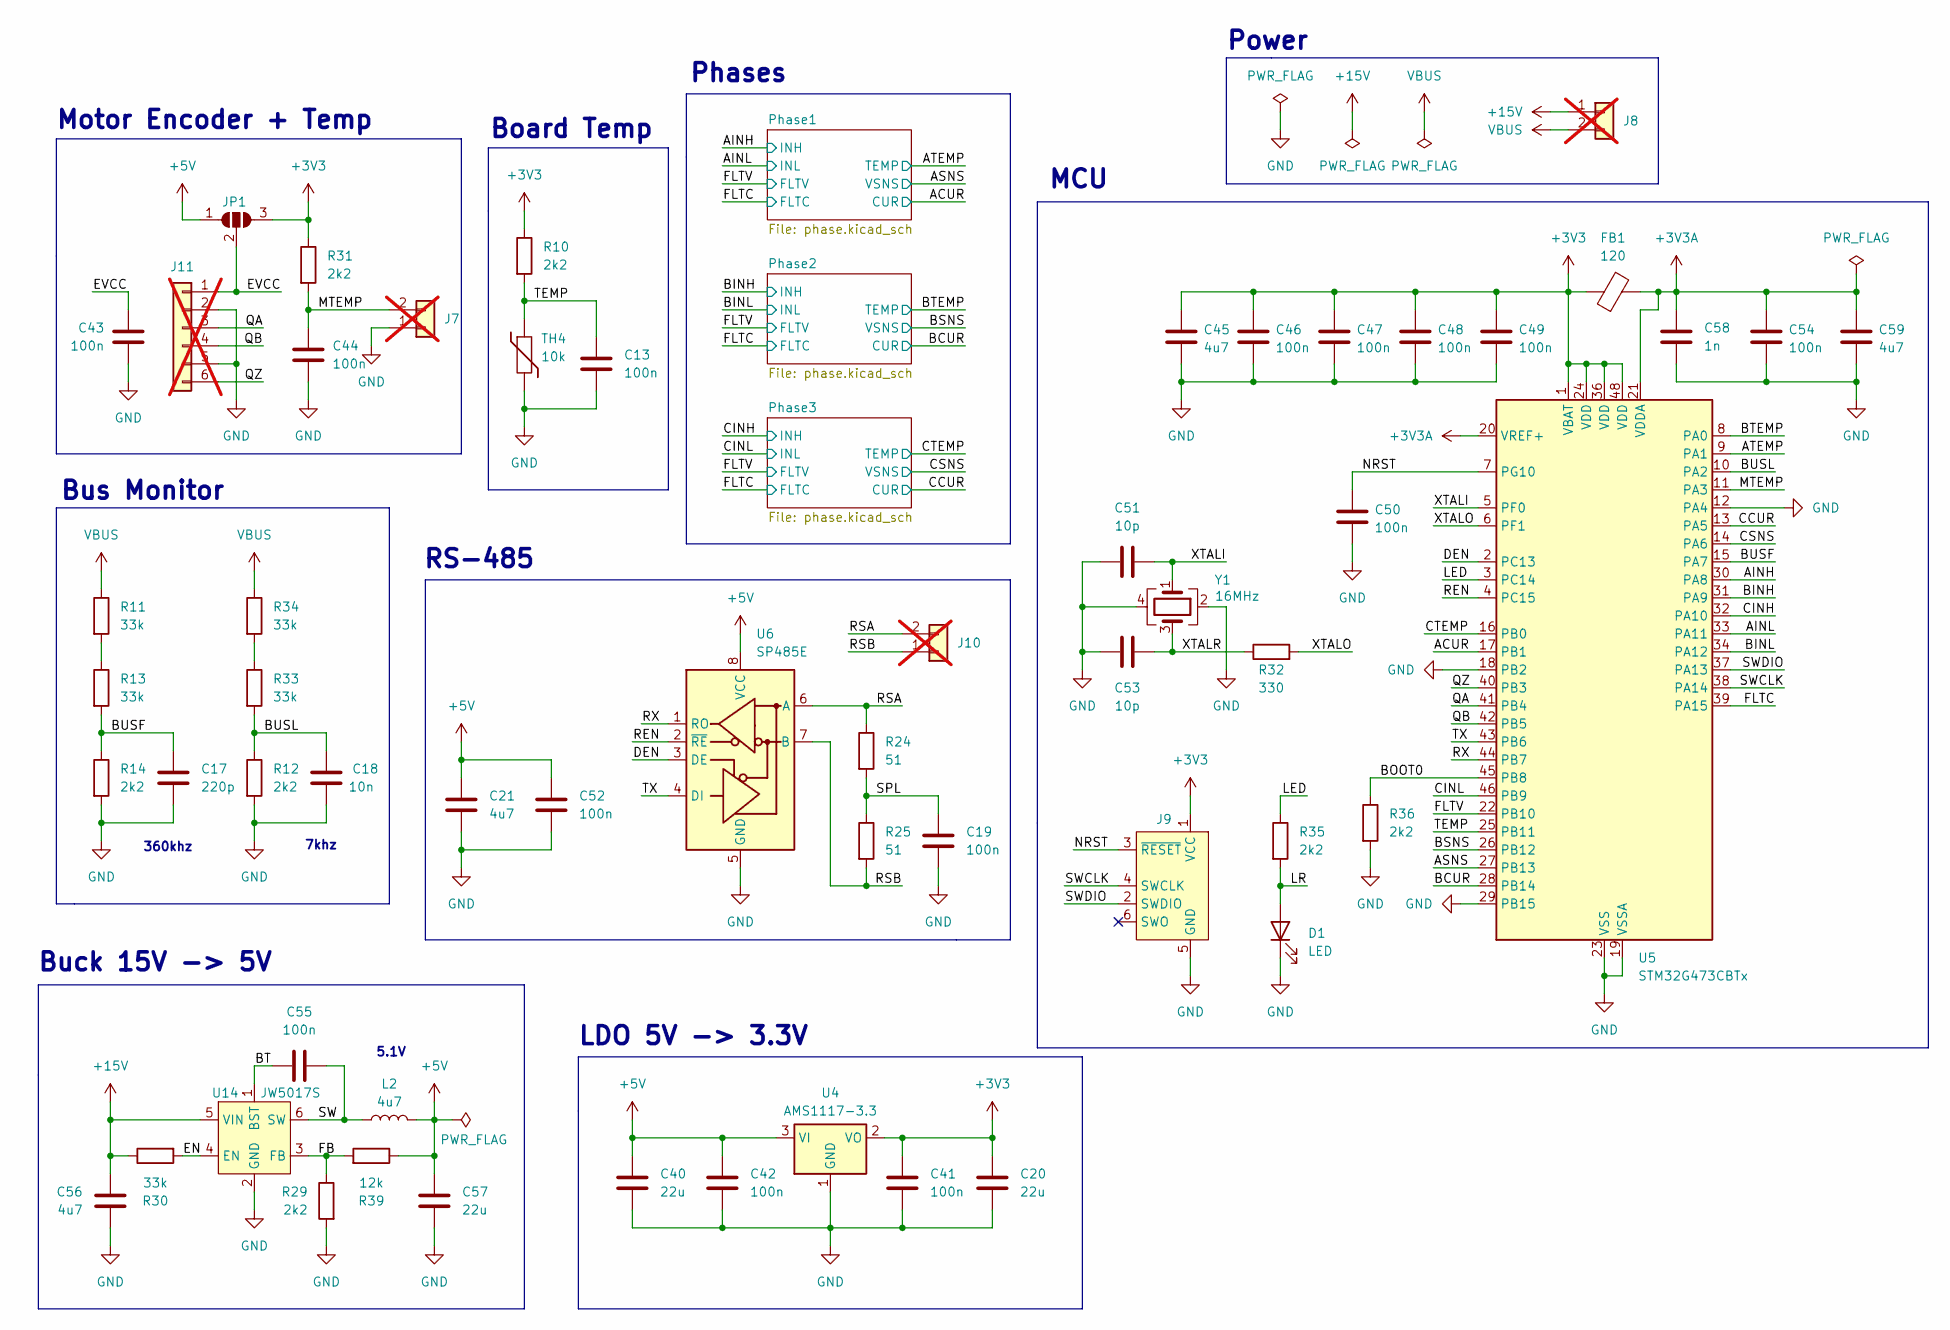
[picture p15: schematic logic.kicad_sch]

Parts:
C13, C19, C41, C42, C43, C44, C46, C47, C48, C49, C50, C52, C54, C55: 100n; C_0402_1005Metric; LCSC C307331
C17: 220p; C_0402_1005Metric; LCSC C1530
C18: 10n; C_0402_1005Metric; LCSC C15195
C20, C40, C57: 22u; C_1206_3216Metric; LCSC C20416445
C21, C45, C56, C59: 4u7; C_0805_2012Metric; LCSC C33546011
C51, C53: 10p; C_0402_1005Metric; LCSC C32949
C58: 1n; C_0402_1005Metric; LCSC C1523
D1: LED; LED_0603_1608Metric; LCSC C2290
FB1: 120; L_0603_1608Metric; LCSC C14709
J7, J8, J10: Conn_01x02; 1x02_2.00mm_Solder; not fitted
J9: Conn_ARM_SWD_TagConnect_TC2030-NL; Tag-Connect_TC2030-IDC-NL_2x03_P1.27mm_Vertical
J11: Conn_01x06; 1x06_2.00mm_Solder; not fitted
JP1: SolderJumper_3_Open; SolderJumper-3_P1.3mm_Open_RoundedPad1.0x1.5mm
L2: 4u7; L_TechFuse_SL0420; LCSC C22463808
R10, R12, R14, R29, R31, R35, R36: 2k2; R_0402_1005Metric; LCSC C25879
R11, R13, R30, R33, R34: 33k; R_0402_1005Metric; LCSC C25779
R24, R25: 51; R_0805_2012Metric; LCSC C17738
R32: 330; R_0402_1005Metric; LCSC C25104
R39: 12k; R_0402_1005Metric; LCSC C25752
TH4: 10k; R_0402_1005Metric; LCSC C41417281
U4: AMS1117-3.3; SOT-223-3_TabPin2; LCSC C6186
U5: STM32G473CBTx; LQFP-48_7x7mm_P0.5mm; LCSC C730111
U6: SP485E; JEITA_SOIC-8_3.9x4.9mm_P1.27mm; LCSC C6855
U14: JW5017S; SOT-23-6; LCSC C371172
Y1: 16MHz; Crystal_SMD_3225-4Pin_3.2x2.5mm; LCSC C13738

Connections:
+3V3: C20.1, C41.1, C45.1, C46.1, C47.1, C48.1, C49.1, FB1.1, J9.1 (VCC), JP1.3 (B), R10.1, R31.1, U4.2 (VO), U5.1 (VBAT), U5.24 (VDD), U5.36 (VDD), U5.48 (VDD); also elsewhere on the board
+3V3A: C54.1, C58.1, C59.1, FB1.2, U5.20 (VREF+), U5.21 (VDDA)
+5V: C21.1, C40.1, C42.1, C52.1, C57.1, JP1.1 (A), L2.2, R39.1, U4.3 (VI), U6.8 (VCC)
+15V: C56.1, J8.1, R30.1, U14.5 (VIN); also elsewhere on the board
/ACUR: U5.17 (PB1); also elsewhere on the board
/AINH: U5.30 (PA8); also elsewhere on the board
/AINL: U5.33 (PA11); also elsewhere on the board
/ASNS: U5.27 (PB13); also elsewhere on the board
/ATEMP: U5.9 (PA1); also elsewhere on the board
/BCUR: U5.28 (PB14); also elsewhere on the board
/BINH: U5.31 (PA9); also elsewhere on the board
/BINL: U5.34 (PA12); also elsewhere on the board
/BOOT0: R36.1, U5.45 (PB8)
/BSNS: U5.26 (PB12); also elsewhere on the board
/BT: C55.1, U14.1 (BST)
/BTEMP: U5.8 (PA0); also elsewhere on the board
/BUSF: C17.1, R13.2, R14.1, U5.15 (PA7)
/BUSL: C18.1, R12.1, R33.2, U5.10 (PA2)
/CCUR: U5.13 (PA5); also elsewhere on the board
/CINH: U5.32 (PA10); also elsewhere on the board
/CINL: U5.46 (PB9); also elsewhere on the board
/CSNS: U5.14 (PA6); also elsewhere on the board
/CTEMP: U5.16 (PB0); also elsewhere on the board
/DEN: U5.2 (PC13), U6.3 (DE)
/EN: R30.2, U14.4 (EN)
/EVCC: C43.1, J11.1, JP1.2 (C)
/FB: R29.1, R39.2, U14.3 (FB)
/FLTC: U5.39 (PA15); also elsewhere on the board
/FLTV: U5.22 (PB10); also elsewhere on the board
/LED: R35.1, U5.3 (PC14)
/LR: D1.2 (A), R35.2
/MTEMP: C44.1, J7.2, R31.2, U5.11 (PA3)
/NRST: C50.1, J9.3 (~RESET), U5.7 (PG10)
/QA: J11.3, U5.41 (PB4)
/QB: J11.4, U5.42 (PB5)
/QZ: J11.6, U5.40 (PB3)
/REN: U5.4 (PC15), U6.2 (~RE)
/RSA: J10.2, R24.1, U6.6 (A)
/RSB: J10.1, R25.2, U6.7 (B)
/RX: U5.44 (PB7), U6.1 (RO)
/SPL: C19.2, R24.2, R25.1
/SW: C55.2, L2.1, U14.6 (SW)
/SWCLK: J9.4 (SWCLK), U5.38 (PA14)
/SWDIO: J9.2 (SWDIO), U5.37 (PA13)
/TEMP: C13.1, R10.2, TH4.1, U5.25 (PB11)
/TX: U5.43 (PB6), U6.4 (DI)
/XTALI: C51.2, U5.5 (PF0), Y1.1
/XTALO: R32.2, U5.6 (PF1)
/XTALR: C53.2, R32.1, Y1.3
GND: C13.2, C17.2, C18.2, C19.1, C20.2, C21.2, C40.2, C41.2, C42.2, C43.2, C44.2, C45.2, C46.2, C47.2, C48.2, C49.2, C50.2, C51.1, C52.2, C53.1, C54.2, C56.2, C57.2, C58.2, C59.2, D1.1 (K), J7.1, J9.5 (GND), J11.2, J11.5, R12.2, R14.2, R29.2, R36.2, TH4.2, U4.1 (GND), U5.12 (PA4), U5.18 (PB2), U5.19 (VSSA), U5.23 (VSS), U5.29 (PB15), U5.35 (VSS), U5.47 (VSS), U6.5 (GND), U14.2 (GND), Y1.2, Y1.4; also elsewhere on the board
unnamed: R11.2, R13.1
unnamed: R33.1, R34.2
VBUS: J8.2, R11.1, R34.1

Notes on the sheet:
Board Temp
Power
Motor Encoder + Temp
5.1V
LDO 5V -> 3.3V
Bus Monitor
RS-485
360khz
Phases
MCU
7khz
Buck 15V -> 5V

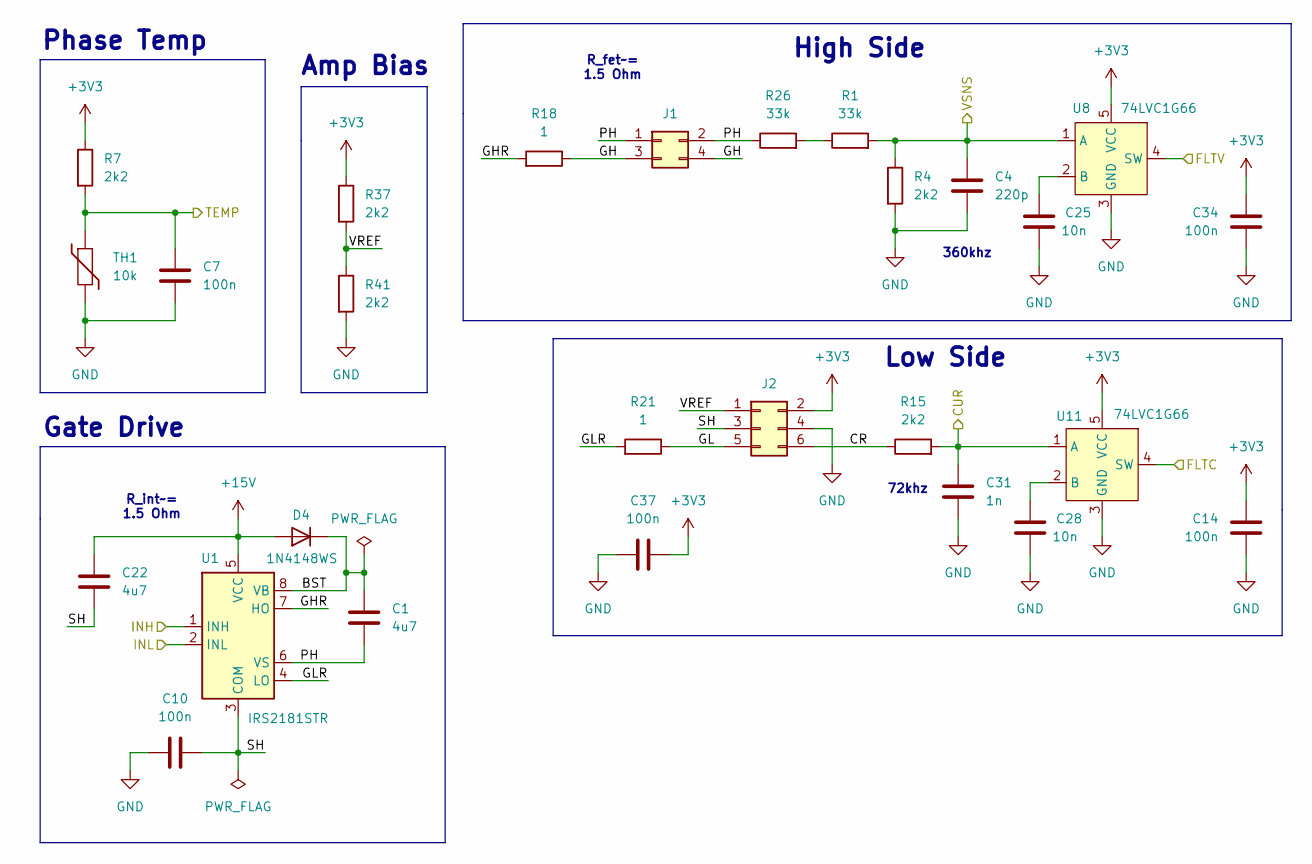
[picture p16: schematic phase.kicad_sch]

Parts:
C1: 4u7; C_1206_3216Metric; LCSC C29823
C4: 220p; C_0402_1005Metric; LCSC C1530
C7, C10, C14, C34, C37: 100n; C_0402_1005Metric; LCSC C307331
C22: 4u7; C_0805_2012Metric; LCSC C33546011
C25, C28: 10n; C_0402_1005Metric; LCSC C15195
C31: 1n; C_0402_1005Metric; LCSC C1523
D4: 1N4148WS; D_SOD-323; LCSC C2128
J1: Conn_02x02_Odd_Even; PinSocket_2x02_P1.27mm_Vertical_SMD; LCSC C30607465
J2: Conn_02x03_Odd_Even; PinSocket_2x03_P1.27mm_Vertical_SMD; LCSC C32713074
R1, R26: 33k; R_0402_1005Metric; LCSC C25779
R4, R7, R15, R37, R41: 2k2; R_0402_1005Metric; LCSC C25879
R18, R21: 1; R_0603_1608Metric; LCSC C22936
TH1: 10k; R_0402_1005Metric; LCSC C41417281
U1: IRS2181STR; JEITA_SOIC-8_3.9x4.9mm_P1.27mm; LCSC C20623180
U8, U11: 74LVC1G66; SOT-23-5; LCSC C46553572

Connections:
+3V3: C14.1, C34.1, C37.2, J2.2, R7.1, R37.1, U8.5 (VCC), U11.5 (VCC); also elsewhere on the board
+15V: C22.1, D4.2 (A), U1.5 (VCC); also elsewhere on the board
/ACUR: C31.1, R15.2, U11.1 (A); also elsewhere on the board
/AINH: U1.1 (INH); also elsewhere on the board
/AINL: U1.2 (INL); also elsewhere on the board
/ASNS: C4.1, R1.2, R4.1, U8.1 (A); also elsewhere on the board
/ATEMP: C7.1, R7.2, TH1.1; also elsewhere on the board
/FLTC: U11.4 (SW); also elsewhere on the board
/FLTV: U8.4 (SW); also elsewhere on the board
/Phase1/BST: C1.1, D4.1 (K), U1.8 (VB)
/Phase1/CR: J2.6, R15.1
/Phase1/GH: J1.3, J1.4, R18.1
/Phase1/GHR: R18.2, U1.7 (HO)
/Phase1/GL: J2.5, R21.1
/Phase1/GLR: R21.2, U1.4 (LO)
/Phase1/PH: C1.2, J1.1, J1.2, R26.1, U1.6 (VS)
/Phase1/SH: C10.2, C22.2, J2.3, U1.3 (COM)
/Phase1/VREF: J2.1, R37.2, R41.1
GND: C4.2, C7.2, C10.1, C14.2, C25.2, C28.2, C31.2, C34.2, C37.1, J2.4, R4.2, R41.2, TH1.2, U8.3 (GND), U11.3 (GND); also elsewhere on the board
unnamed: R1.1, R26.2
unnamed: C25.1, U8.2 (B)
unnamed: C28.1, U11.2 (B)

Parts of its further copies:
C2, C3: 4u7; C_1206_3216Metric; LCSC C29823
C5, C6: 220p; C_0402_1005Metric; LCSC C1530
C8, C9, C11, C12, C15, C16, C35, C36, C38, C39: 100n; C_0402_1005Metric; LCSC C307331
C23, C24: 4u7; C_0805_2012Metric; LCSC C33546011
C26, C27, C29, C30: 10n; C_0402_1005Metric; LCSC C15195
C32, C33: 1n; C_0402_1005Metric; LCSC C1523
D5, D6: 1N4148WS; D_SOD-323; LCSC C2128
J3, J5: Conn_02x02_Odd_Even; PinSocket_2x02_P1.27mm_Vertical_SMD; LCSC C30607465
J4, J6: Conn_02x03_Odd_Even; PinSocket_2x03_P1.27mm_Vertical_SMD; LCSC C32713074
R2, R3, R27, R28: 33k; R_0402_1005Metric; LCSC C25779
R5, R6, R8, R9, R16, R17, R38, R40, R42, R43: 2k2; R_0402_1005Metric; LCSC C25879
R19, R20, R22, R23: 1; R_0603_1608Metric; LCSC C22936
TH2, TH3: 10k; R_0402_1005Metric; LCSC C41417281
U2, U3: IRS2181STR; JEITA_SOIC-8_3.9x4.9mm_P1.27mm; LCSC C20623180
U9, U10, U12, U13: 74LVC1G66; SOT-23-5; LCSC C46553572

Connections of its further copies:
+3V3: C15.1, C16.1, C35.1, C36.1, C38.2, C39.2, J4.2, J6.2, R8.1, R9.1, R38.1, R40.1, U9.5 (VCC), U10.5 (VCC), U12.5 (VCC), U13.5 (VCC); also elsewhere on the board
+15V: C23.1, C24.1, D5.2 (A), D6.2 (A), U2.5 (VCC), U3.5 (VCC); also elsewhere on the board
/BCUR: C32.1, R16.2, U12.1 (A); also elsewhere on the board
/BINH: U2.1 (INH); also elsewhere on the board
/BINL: U2.2 (INL); also elsewhere on the board
/BSNS: C5.1, R2.2, R5.1, U9.1 (A); also elsewhere on the board
/BTEMP: C8.1, R8.2, TH2.1; also elsewhere on the board
/CCUR: C33.1, R17.2, U13.1 (A); also elsewhere on the board
/CINH: U3.1 (INH); also elsewhere on the board
/CINL: U3.2 (INL); also elsewhere on the board
/CSNS: C6.1, R3.2, R6.1, U10.1 (A); also elsewhere on the board
/CTEMP: C9.1, R9.2, TH3.1; also elsewhere on the board
/FLTC: U12.4 (SW), U13.4 (SW); also elsewhere on the board
/FLTV: U9.4 (SW), U10.4 (SW); also elsewhere on the board
/Phase2/BST: C2.1, D5.1 (K), U2.8 (VB)
/Phase2/CR: J4.6, R16.1
/Phase2/GH: J3.3, J3.4, R19.1
/Phase2/GHR: R19.2, U2.7 (HO)
/Phase2/GL: J4.5, R22.1
/Phase2/GLR: R22.2, U2.4 (LO)
/Phase2/PH: C2.2, J3.1, J3.2, R27.1, U2.6 (VS)
/Phase2/SH: C11.2, C23.2, J4.3, U2.3 (COM)
/Phase2/VREF: J4.1, R38.2, R42.1
/Phase3/BST: C3.1, D6.1 (K), U3.8 (VB)
/Phase3/CR: J6.6, R17.1
/Phase3/GH: J5.3, J5.4, R20.1
/Phase3/GHR: R20.2, U3.7 (HO)
/Phase3/GL: J6.5, R23.1
/Phase3/GLR: R23.2, U3.4 (LO)
/Phase3/PH: C3.2, J5.1, J5.2, R28.1, U3.6 (VS)
/Phase3/SH: C12.2, C24.2, J6.3, U3.3 (COM)
/Phase3/VREF: J6.1, R40.2, R43.1
GND: C5.2, C6.2, C8.2, C9.2, C11.1, C12.1, C15.2, C16.2, C26.2, C27.2, C29.2, C30.2, C32.2, C33.2, C35.2, C36.2, C38.1, C39.1, J4.4, J6.4, R5.2, R6.2, R42.2, R43.2, TH2.2, TH3.2, U9.3 (GND), U10.3 (GND), U12.3 (GND), U13.3 (GND); also elsewhere on the board
unnamed: R2.1, R27.2
unnamed: R3.1, R28.2
unnamed: C26.1, U9.2 (B)
unnamed: C27.1, U10.2 (B)
unnamed: C29.1, U12.2 (B)
unnamed: C30.1, U13.2 (B)

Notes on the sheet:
Low Side
R_fet~= 1.5 Ohm
Amp Bias
R_int~= 1.5 Ohm
Gate Drive
Phase Temp
72khz
360khz
High Side

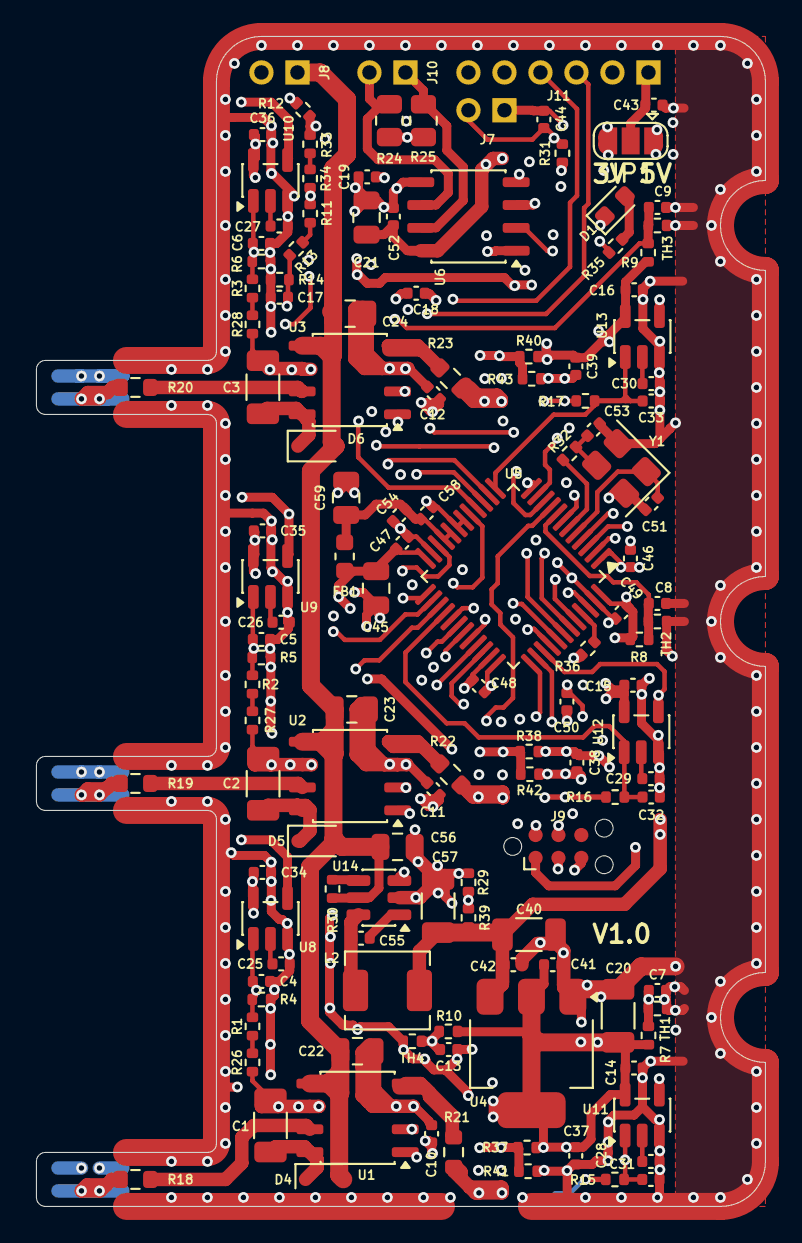
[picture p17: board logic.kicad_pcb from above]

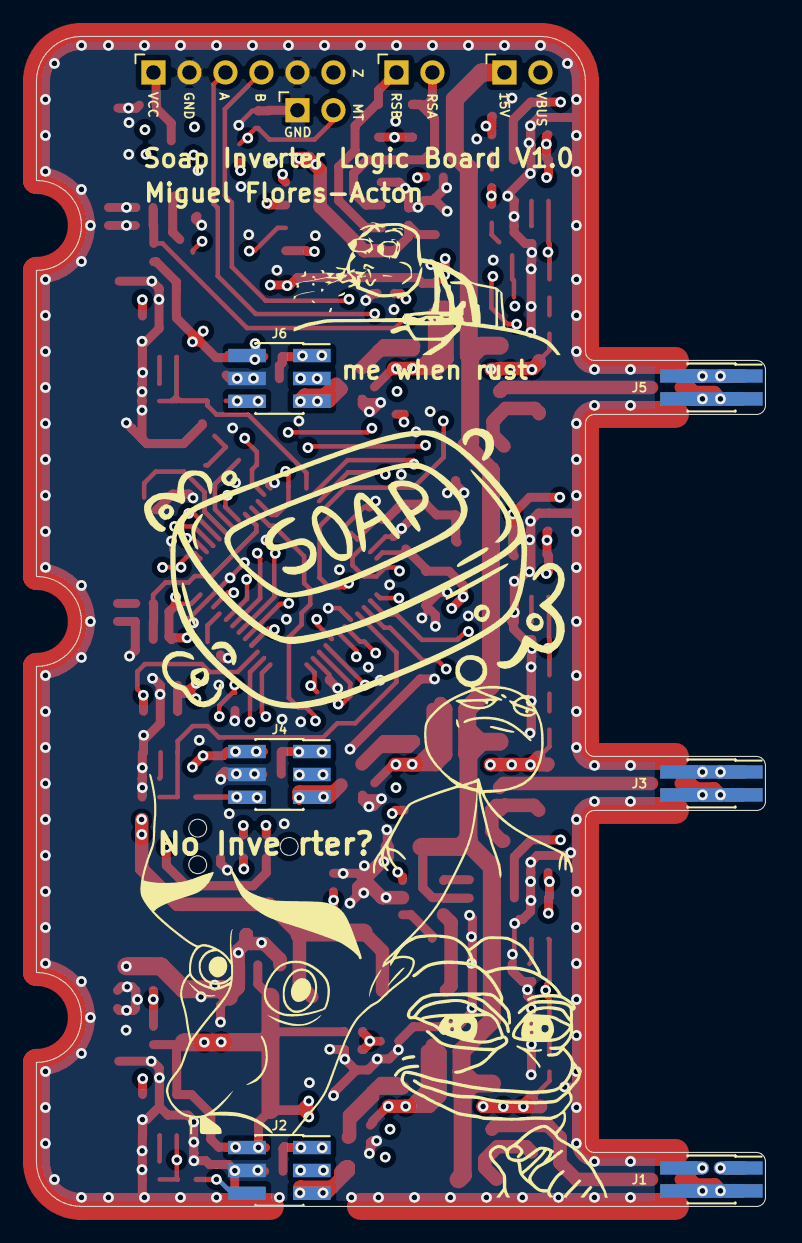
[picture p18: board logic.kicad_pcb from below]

Board: 4 copper layers, 40.5 x 65.0 mm, 143 parts (15 on the bottom side), 89 nets.

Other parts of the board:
G1, G2, G3, G4, G5: LOGO

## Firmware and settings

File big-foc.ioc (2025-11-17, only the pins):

Mcu.UserName=STM32G473CBTx
PA0.Signal=ADC1_IN1
PA1.Signal=ADC1_IN2
PA10.Signal=S_TIM1_CH3
PA11.Signal=TIM1_CH1N
PA12.Signal=TIM1_CH2N
PA13.Signal=SYS_JTMS-SWDIO
PA14.Signal=SYS_JTCK-SWCLK
PA15.Signal=GPIO_Output
PA2.Signal=ADC1_IN3
PA3.Signal=ADC1_IN4
PA4.GPIO_Label=GND
PA4.Signal=GPIO_Output
PA5.Signal=ADC2_IN13
PA6.Signal=ADC2_IN3
PA7.Signal=COMP2_INP
PA8.Signal=S_TIM1_CH1
PA9.Signal=S_TIM1_CH2
PB0.Signal=ADC1_IN15
PB1.Signal=ADC3_IN1
PB10.Signal=GPIO_Output
PB11.Signal=ADC1_IN14
PB12.Signal=ADC4_IN3
PB13.Signal=ADC3_IN5
PB14.Signal=ADC4_IN4
PB15.GPIO_Label=GND
PB15.Signal=GPIO_Output
PB2.GPIO_Label=GND
PB2.Signal=GPIO_Output
PB3.Signal=S_TIM3_ETR
PB4.Signal=S_TIM3_CH1
PB5.Signal=S_TIM3_CH2
PB6.Signal=USART1_TX
PB7.Signal=USART1_RX
PB9.Signal=TIM1_CH3N
PC13.Signal=GPIO_Output
PC14-OSC32_IN.Signal=GPIO_Output
PC15-OSC32_OUT.Signal=GPIO_Output
PF0-OSC_IN.Signal=RCC_OSC_IN
PF1-OSC_OUT.Signal=RCC_OSC_OUT

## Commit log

2025-11-04 Prototype layout
    [drive.kicad_pcb, drive.kicad_sch, phase.kicad_sch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]
2025-11-09 Semifinish power and bulk
    [bom.csv, bulk.kicad_pcb, bulk.kicad_sch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]
2025-11-09 Generate step
    [power.step]
2025-11-10 Save progress
    [assembly.fcstd, bulk.kicad_pcb, logic.kicad_pcb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]
2025-11-10 Update shunts
    [phase.kicad_sch, power.kicad_pcb]
2025-11-13 Add connectors
2025-11-17 Finish rev 1
    [bom.csv, bulk.kicad_pcb, bulk.kicad_sch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]
